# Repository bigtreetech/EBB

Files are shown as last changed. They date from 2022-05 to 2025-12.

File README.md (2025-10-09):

# [切换到中文版](./README_zh_cn.md)

# EBB36 & 42 CAN V1.0
## Hardware
* MCU: ARM Cortex-M0 STM32F072C8T6 48MHz with CAN bus
* Stepper Dirver: Onboard TMC2209 in UART mode, UART address: 00, Rsense: 0.11R
* Onboard Accelerometer Sensor: ADXL345
* Onboard Temperature IC: Max31865 Select 2 / 4 lines PT100 / PT1000 by DIP switch (no Max31865 verson have not this feature)
* Input Voltage: DC12V-DC24V 6A
* Logic Voltage: DC 3.3V
* Heating Interface: Hotend (E0), maximum output current: 5A
* Fan Interfaces: two CNC fans (FAN0, FAN1)
* Maximum Output Current of Fan Interface: 1A, Peak Value 1.5A
* Expansion Interfaces: EndStop, I2C, Probe, RGB, PT100/PT1000, USB interface, CAN Interface
* Temperature Sensor Interface Optional: 1 Channel 100K NTC or PT1000(TH0), 1 Channel PT100/PT1000
* USB Communication Interface: USB-Type-C
* DC 5V Maximum Output Current: 1A

## Firmware
* Only supports Klipper at the present.

## Pinout
* EBB36 CAN V1.0
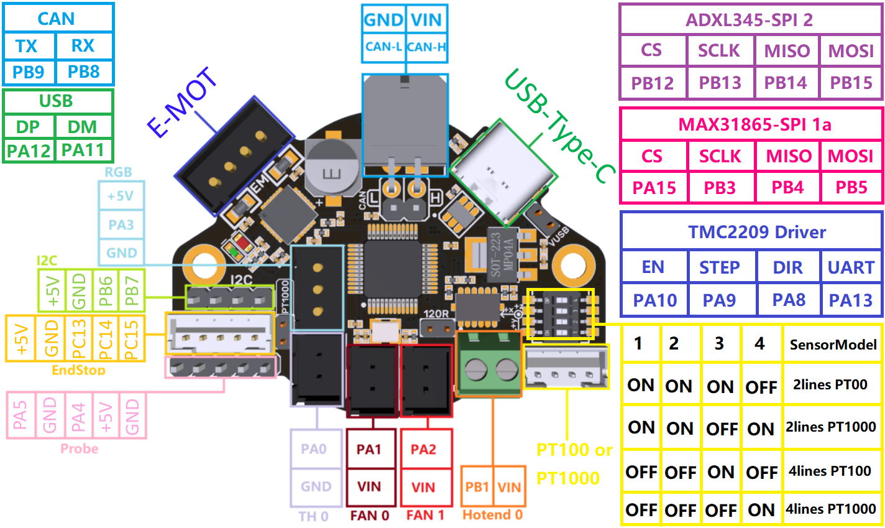
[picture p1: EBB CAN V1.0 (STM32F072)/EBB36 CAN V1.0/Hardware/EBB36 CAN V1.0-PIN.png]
  <br/><br/>
* EBB42 CAN V1.0
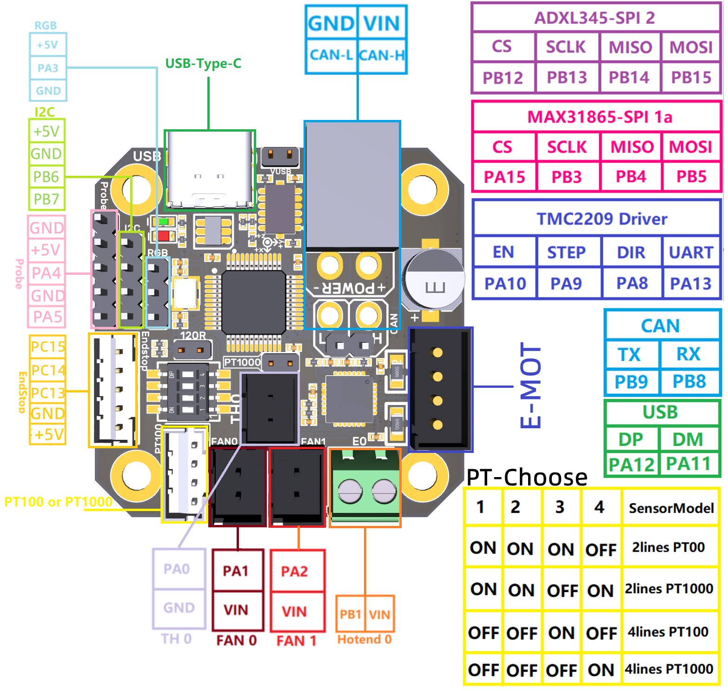
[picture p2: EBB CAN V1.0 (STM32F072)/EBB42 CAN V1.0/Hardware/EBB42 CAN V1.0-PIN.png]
  <br/><br/>

## Build Firmware Image
1. Precompiled firmware(The source code version used is [Commits on Nov 20, 2023](https://github.com/Klipper3d/klipper/commit/bb4711c5d31e8159945f945c662e6668059a174f))
   * [firmware_USB.bin](./EBB%20CAN%20V1.0%20(STM32F072)/firmware_USB.bin) Use USB to communicate with raspberry pi / BTT Pi.
   * [firmware_canbus.bin](./EBB%20CAN%20V1.0%20(STM32F072)/firmware_canbus.bin) Use CAN bus to communicate with raspberry pi / BTT Pi, baudrate = 1000K.

3. Build your own firmware<br/>
   1. Refer to [klipper's official installation](https://www.klipper3d.org/Installation.html) to download klipper source code to raspberry pi
   2. `Building the micro-controller` with the configuration shown below.
      * [*] Enable extra low-level configuration options
      * Micro-controller Architecture = `STMicroelectronics STM32`
      * Processor model = `STM32F072`
      * IF USE CanBoot
         * Bootloader offset = `8KiB bootloader`
      * ELSE
         * Bootloader offset = `No bootloader`
      * Clock Reference = `8 MHz crystal`
      * IF USE USB
         * Communication interface = `USB (on PA11/PA12)`
      * ElSE IF USE CAN bus
         * Communication interface = `CAN bus (on PB8/PB9)`
         * `(1000000)` CAN bus speed

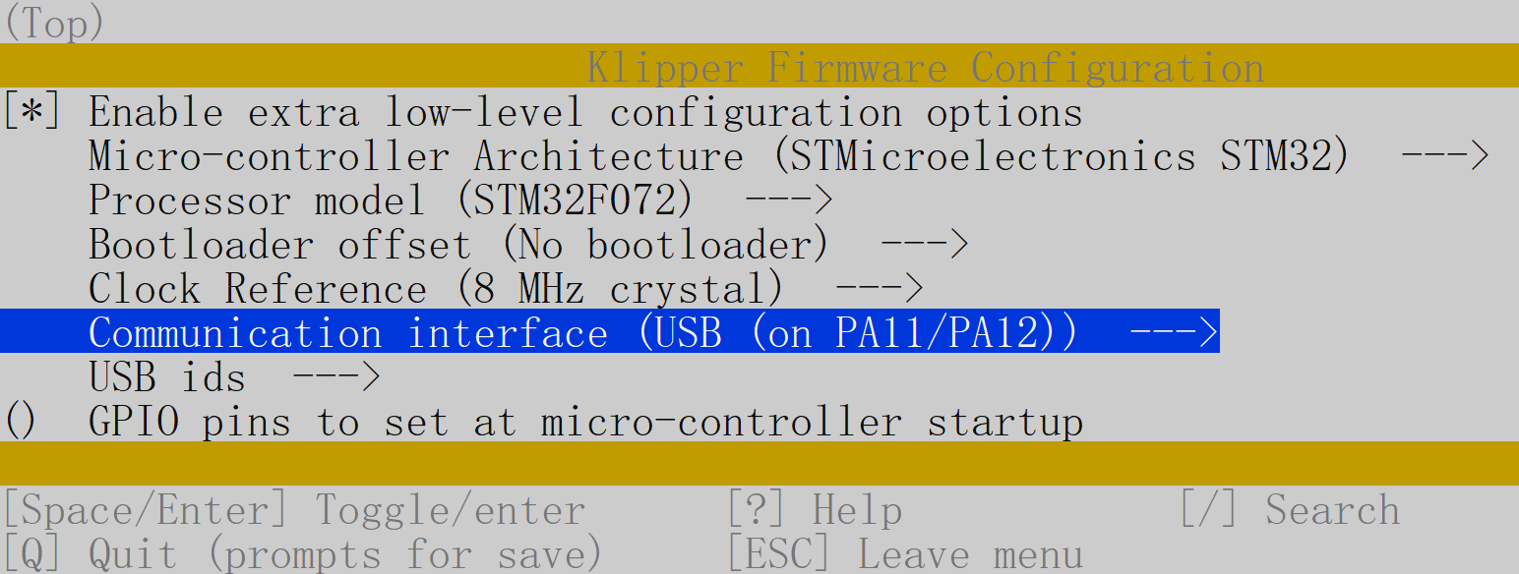
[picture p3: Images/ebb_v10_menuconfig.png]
      <br/>
   3. Once the configuration is selected, press `q` to exit,  and "Yes" when  asked to save the configuration.
   4. Run the command `make`
   5. The `klipper.bin` file will be generated in the folder `home/pi/kliiper/out` when the `make` command completed. And you can use the windows computer under the same LAN as raspberry pi to copy `klipper.bin` from raspberry pi to the computer with `pscp` command in the CMD terminal. such as `pscp -C pi@192.168.0.101:/home/pi/klipper/out/klipper.bin c:\klipper.bin`(The terminal may prompt that `The server's host key is not cached` and ask `Store key in cache?((y/n)`, Please type `y` to store. And then it will ask for a password, please type the default password `raspberry` for raspberry pi)

## board.cfg files
   * [sample-bigtreetech-ebb-canbus-v1.0.cfg](./EBB%20CAN%20V1.0%20(STM32F072)/sample-bigtreetech-ebb-canbus-v1.0.cfg) includes all the correct pinout for EBB36 & 42 CAN V1.0

# EBB36 & 42 CAN V1.1 and V1.2
## Hardware
* MCU: ARM Cortex-M0+ STM32G0B1CBT6 64MHz whit FDCAN bus
* All other parameters are the same as EBB36 & 42 CAN V1.0

## Firmware
* Only supports Klipper at the present.

## Pinout
* EBB36 CAN V1.1 and V1.2
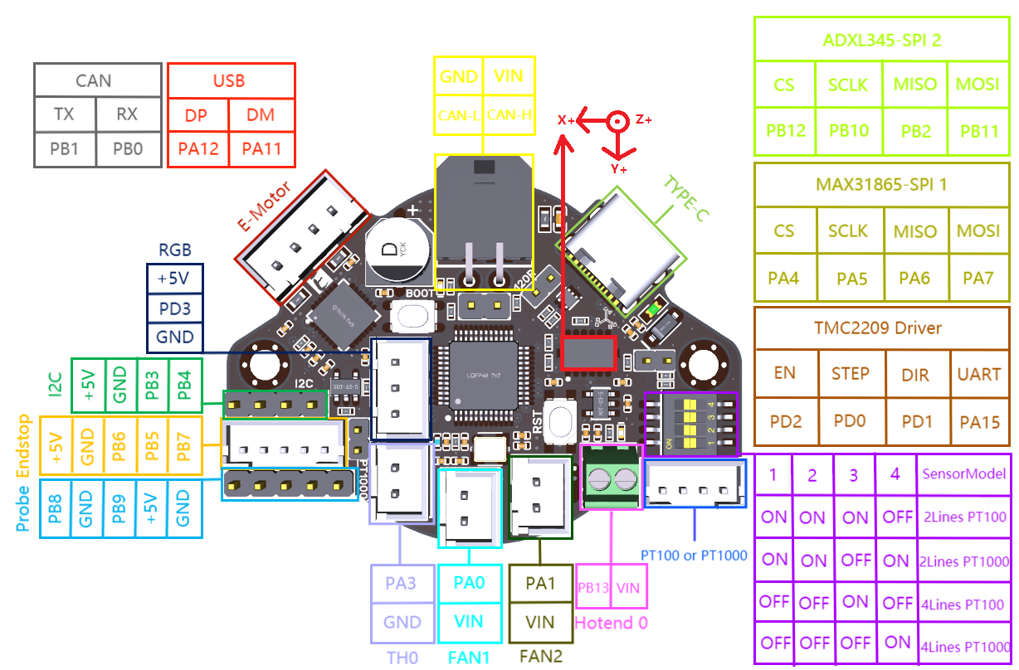
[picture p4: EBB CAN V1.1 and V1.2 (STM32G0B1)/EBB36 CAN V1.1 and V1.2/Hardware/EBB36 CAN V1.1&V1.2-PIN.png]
  <br/><br/>
* EBB42 CAN V1.1 and V1.2
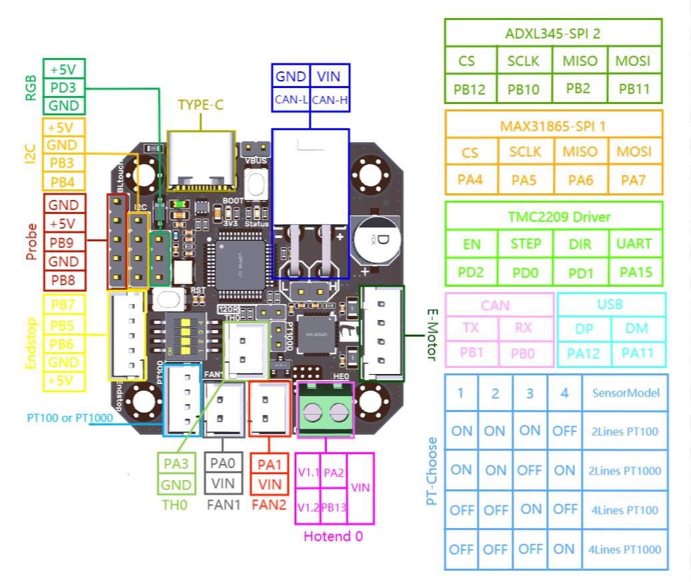
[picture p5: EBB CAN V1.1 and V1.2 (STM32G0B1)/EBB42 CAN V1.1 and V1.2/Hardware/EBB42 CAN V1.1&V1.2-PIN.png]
  <br/><br/>

## Build Firmware Image
1. Precompiled firmware(The source code version used is [Commits on Nov 20, 2023](https://github.com/Klipper3d/klipper/commit/bb4711c5d31e8159945f945c662e6668059a174f))
   * [firmware_USB.bin](./EBB%20CAN%20V1.1%20and%20V1.2%20(STM32G0B1)/firmware_USB.bin) Use USB to communicate with raspberry pi.
   * [firmware_canbus.bin](./EBB%20CAN%20V1.1%20and%20V1.2%20(STM32G0B1)/firmware_canbus.bin) Use CAN bus to communicate with raspberry pi, baudrate = 1000K.

3. Build your own firmware<br/>
   1. Refer to [klipper's official installation](https://www.klipper3d.org/Installation.html) to download klipper source code to raspberry pi
   2. `Building the micro-controller` with the configuration shown below.
      * [*] Enable extra low-level configuration options
      * Micro-controller Architecture = `STMicroelectronics STM32`
      * Processor model = `STM32G0B1`
      * IF USE CanBoot
         * Bootloader offset = `8KiB bootloader`
      * ELSE
         * Bootloader offset = `No bootloader`
      * Clock Reference = `8 MHz crystal`
      * IF USE USB
         * Communication interface = `USB (on PA11/PA12)`
      * ElSE IF USE CAN bus
         * Communication interface = `CAN bus (on PB0/PB1)`
         * `(1000000)` CAN bus speed

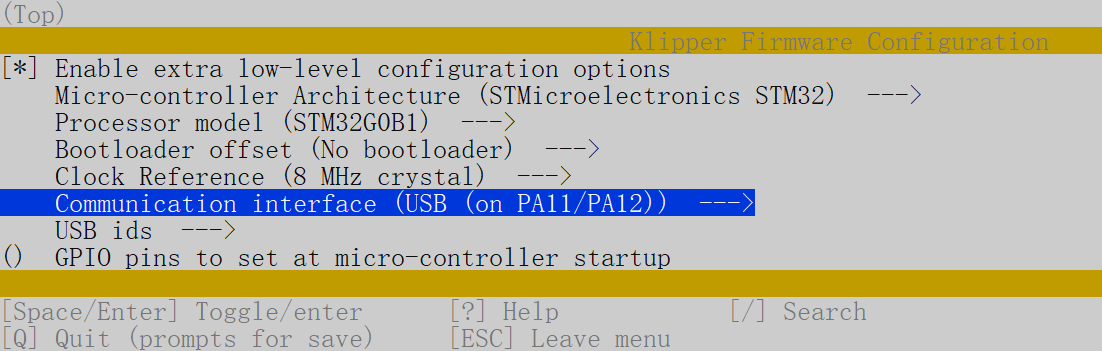
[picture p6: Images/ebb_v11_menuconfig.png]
      <br/>
   3. Once the configuration is selected, press `q` to exit,  and "Yes" when  asked to save the configuration.
   4. Run the command `make`
   5. The `klipper.bin` file will be generated in the folder `home/pi/kliiper/out` when the `make` command completed. And you can use the windows computer under the same LAN as raspberry pi to copy `klipper.bin` from raspberry pi to the computer with `pscp` command in the CMD terminal. such as `pscp -C pi@192.168.0.101:/home/pi/klipper/out/klipper.bin c:\klipper.bin`(The terminal may prompt that `The server's host key is not cached` and ask `Store key in cache?((y/n)`, Please type `y` to store. And then it will ask for a password, please type the default password `raspberry` for raspberry pi)

## Firmware update
### Warning: <br/>
(Only for EBB 36/42 CAN V1.1)<br/>
__STM32G0B1CB needs to jump to the System memory area to run bootloader (written by STMicroelectronics) when using DFU to update firmware through the Type-C port. Referring to the description in manual [AN2606](https://www.st.com/content/ccc/resource/technical/document/application_note/b9/9b/16/3a/12/1e/40/0c/CD00167594.pdf/files/CD00167594.pdf/jcr:content/translations/en.C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), The initialization process of this bootloader is shown in the following figure:__
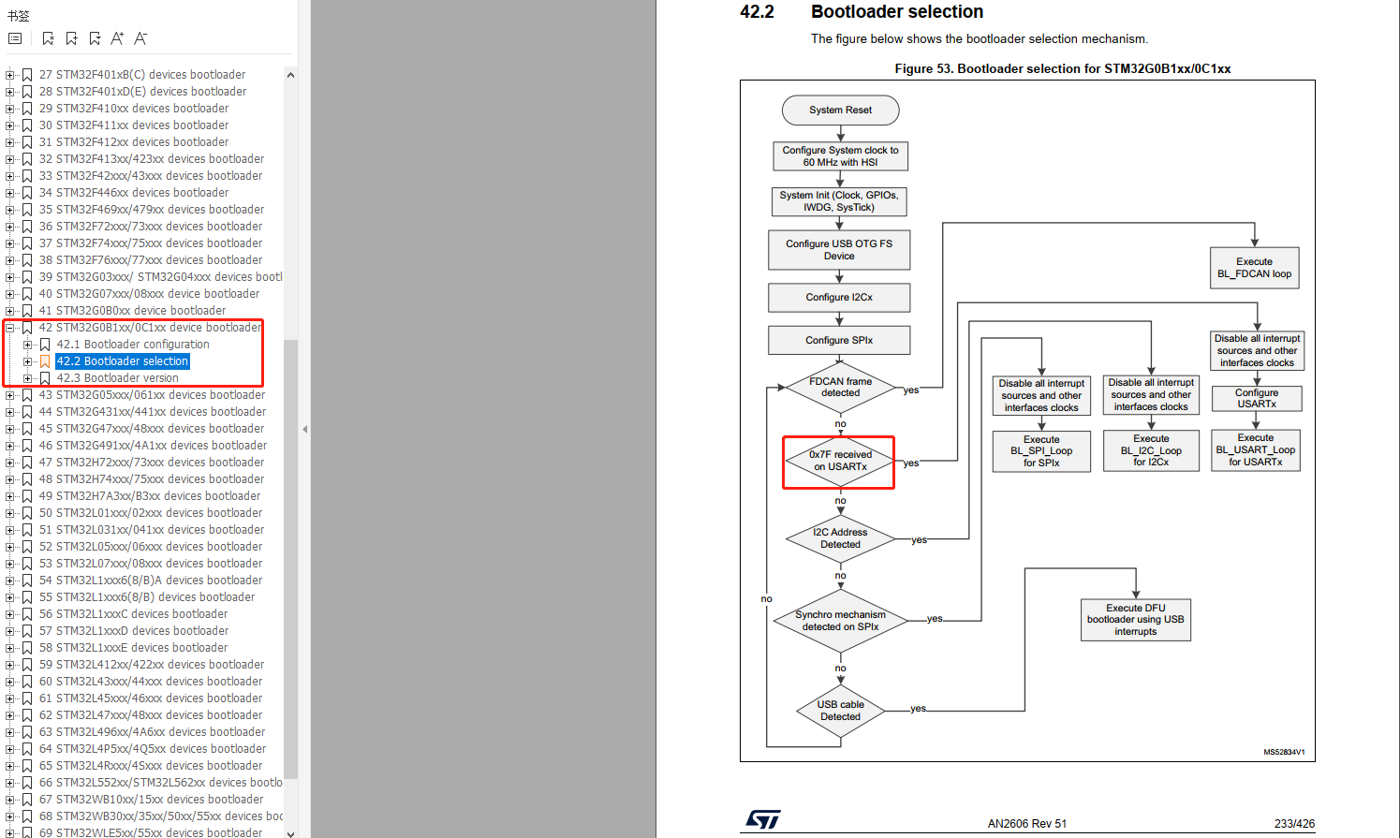
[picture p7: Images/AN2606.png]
  <br/><br/>
__The IO of USART will be configured before going to the USB DFU mode.__<br/>
__After going to DFU mode, PA2 will be configured to output high level by bootloader in System memory area refer to the [datasheet of STM32G0B1CB](https://www.st.com/resource/en/datasheet/stm32g0b1cb.pdf)__
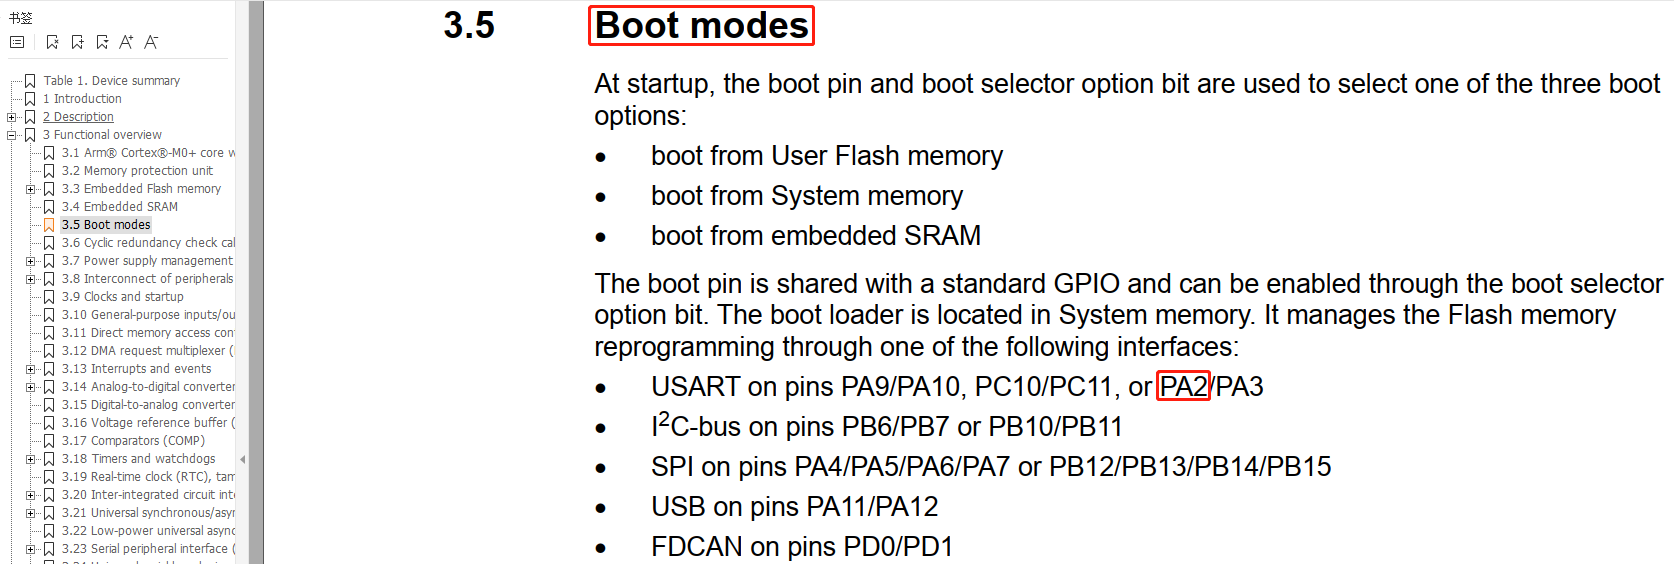
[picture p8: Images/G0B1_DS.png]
  <br/><br/>
__PA2 is used for the hotend MOSFET in EBB36 & 42 CAN V1.1, The high level in the DFU mode change the hotend into heating state. Therefore, please pay attention to disconnect the main power VIN of the hotend when using the DFU of Type-C port to update the firmware, or ensure that the firmware update is completed soon and goto the normal working mode. Never keep MCU in DFU mode for a long time when the main power supply and hotend are connected.__
## board.cfg files
   * [sample-bigtreetech-ebb-canbus-v1.1.cfg](./EBB%20CAN%20V1.1%20and%20V1.2%20(STM32G0B1)/sample-bigtreetech-ebb-canbus-v1.1.cfg) includes all the correct pinout for EBB CAN 36&42 V1.1

# EBB36 & 42 CAN V1.2
__V1.2 compared with v1.1: only the IO of hotend is changed from `PA2` to `PB13`__

## board.cfg files
   * [sample-bigtreetech-ebb-canbus-v1.2.cfg](./EBB%20CAN%20V1.1%20and%20V1.2%20(STM32G0B1)/sample-bigtreetech-ebb-canbus-v1.2.cfg) includes all the correct pinout for EBB CAN 36&42 V1.2

# EBB SB2240_2209 CAN V1.0
## Hardware
* MCU: ARM Cortex-M0+ STM32G0B1CBT6 64MHz whit FDCAN bus
* Stepper Dirver:
   * TMC2209 Version: Onboard TMC2209 in UART mode, UART address: 00, Rsense: 0.11R
   * TMC2240 Version: Onboard TMC2240 in SPI mode
* Onboard Accelerometer Sensor: ADXL345
* Onboard Temperature IC: Max31865 Select 2 / 4 lines PT100 / PT1000 by DIP switch
* Input Voltage: DC12V-DC24V 9A
* Logic Voltage: DC 3.3V
* Heating Interface: Hotend (E0), maximum output current: 5A
* Fan Interfaces:
   * 2 x CNC fans (FAN1, FAN2)
   * 1 x 4-wire fan (4W_FAN)
* Maximum Output Current of Fan Interface: 1A, Peak Value 1.5A
* Expansion Interfaces: EndStop, Bltouch, Proximity(NPN & PNP), RGB, PT100/PT1000, USB, CAN, SPI
* Temperature Sensor Interface Optional: 1 Channel 100K NTC or PT1000(TH0), 1 Channel PT100/PT1000 (Max31865)
* USB Communication Interface: USB-Type-C
* DC 5V Maximum Output Current: 1A

## Firmware
* Only supports Klipper at the present.

## Pinout
* EBB SB2240 CAN V1.0
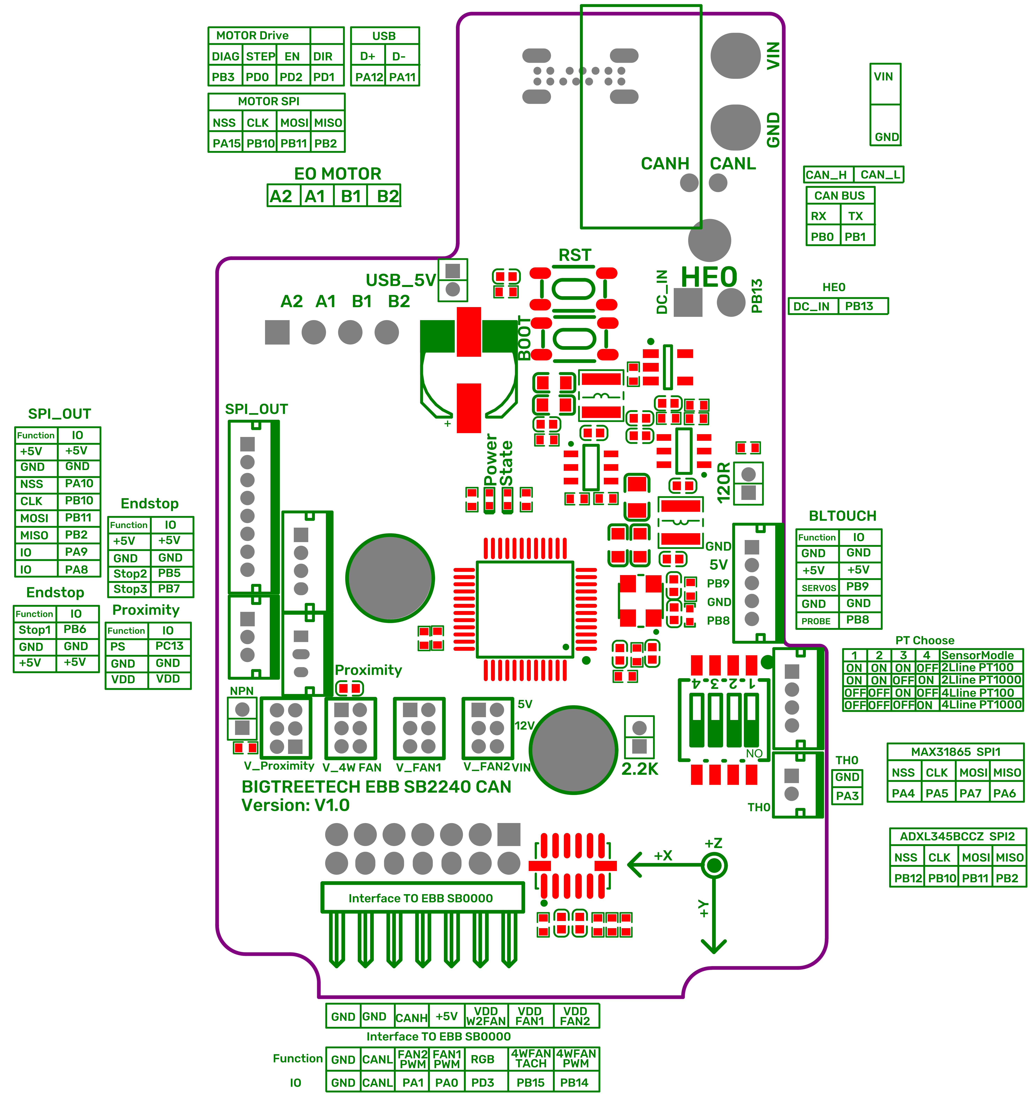
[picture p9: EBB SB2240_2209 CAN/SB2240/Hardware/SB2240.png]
  <br/><br/>
* EBB SB2209 CAN V1.0
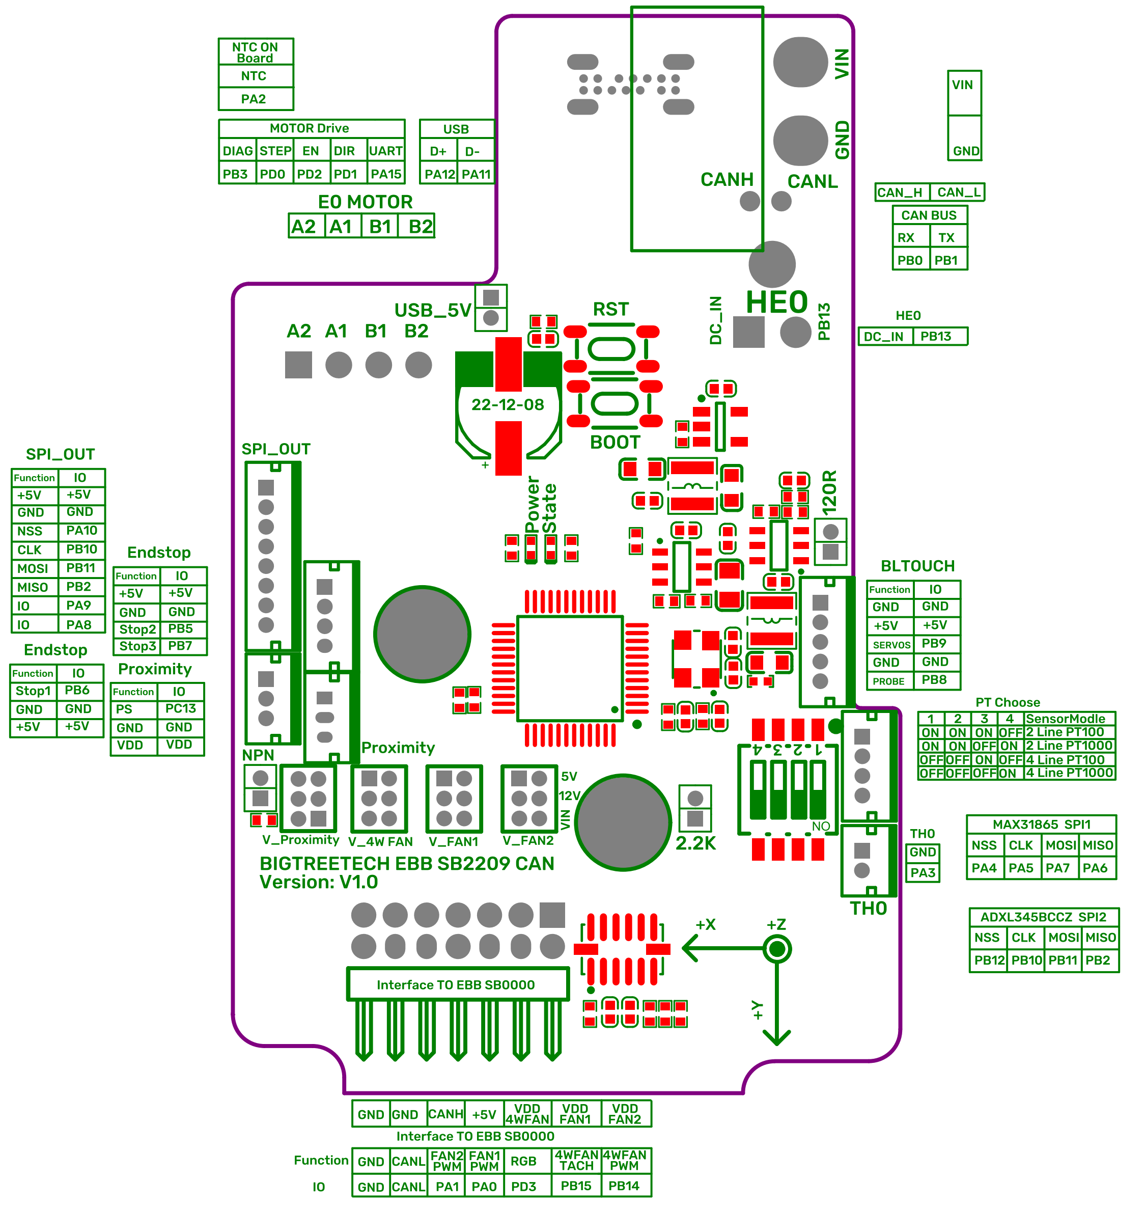
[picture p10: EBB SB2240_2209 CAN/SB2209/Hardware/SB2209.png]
  <br/><br/>

## Build Firmware Image
1. Precompiled firmware(The source code version used is [Commits on Jan 8, 2023](https://github.com/Klipper3d/klipper/commit/bca2671efb8ae6035bb8600619b7a7c4e76169c3))
   * [firmware_USB.bin](./EBB%20SB2240_2209%20CAN/firmware_USB.bin) Use USB to communicate with host.
   * [firmware_canbus.bin](./EBB%20SB2240_2209%20CAN/firmware_canbus.bin) Use CAN bus to communicate with host, baudrate = 1M.
   * [firmware_canbus_8k_bootloader.bin](./EBB%20SB2240_2209%20CAN/firmware_canbus_8k_bootloader.bin) Use CAN bus to communicate with host, baudrate = 1M, 8KB bootloader for Canboot.

3. Build your own firmware<br/>
   1. Refer to [klipper's official installation](https://www.klipper3d.org/Installation.html) to download klipper source code to host
   2. `Building the micro-controller` with the configuration shown below.
      * [*] Enable extra low-level configuration options
      * Micro-controller Architecture = `STMicroelectronics STM32`
      * Processor model = `STM32G0B1`
      * IF USE CanBoot
         * Bootloader offset = `8KiB bootloader`
      * ELSE
         * Bootloader offset = `No bootloader`
      * Clock Reference = `8 MHz crystal`
      * IF USE USB
         * Communication interface = `USB (on PA11/PA12)`
      * ElSE IF USE CAN bus
         * Communication interface = `CAN bus (on PB0/PB1)`
      * (1000000) CAN bus speed

      <br/>
   3. Once the configuration is selected, press `q` to exit,  and "Yes" when  asked to save the configuration.
   4. Run the command `make`
   5. The `klipper.bin` file will be generated in the folder `home/pi/kliiper/out` when the `make` command completed. And you can use the windows computer under the same LAN as host to copy `klipper.bin` from host to the computer with `pscp` command in the CMD terminal. such as `pscp -C pi@192.168.0.101:/home/pi/klipper/out/klipper.bin c:\klipper.bin`(The terminal may prompt that `The server's host key is not cached` and ask `Store key in cache?((y/n)`, Please type `y` to store. And then it will ask for a password, please type the default password `raspberry` for raspberry pi or `biqu` for CB1)

## board.cfg files
   * [sample-bigtreetech-ebb-sb-canbus-v1.0.cfg](./EBB%20SB2240_2209%20CAN/sample-bigtreetech-ebb-sb-canbus-v1.0.cfg) includes all the correct pinout for EBB SB2240_2209 CAN V1.0
   * TMC2209 Version: uncomment tmc2209 config and comment tmc2240 config
      ```
      [tmc2209 extruder]
      uart_pin: EBBCan: PA15
      run_current: 0.650
      stealthchop_threshold: 999999

      # [tmc2240 extruder]
      # cs_pin: EBBCan: PA15
      # spi_bus: spi2_PB2_PB11_PB10
      # run_current: 0.650
      # stealthchop_threshold: 999999
      ```
   * TMC2240 Version: uncomment tmc2240 config and comment tmc2209 config
      ```
      # [tmc2209 extruder]
      # uart_pin: EBBCan: PA15
      # run_current: 0.650
      # stealthchop_threshold: 999999

      [tmc2240 extruder]
      cs_pin: EBBCan: PA15
      # spi_bus: spi2_PB2_PB11_PB10
      driver_TPFD: 0
      run_current: 0.650
      stealthchop_threshold: 999999
      ```

# Note
## Here’s BIGTREETECH! For Makers, by makers!
* We appreciate all of your support to BIGTREETECH! To offer an excellent experience of creation to every makers,We’re devoted to design and produce high-quality and durable accessories!

## How to contact:
### If you have any technical issue,please don’t hesitate contact us:
* BIGTREETECH: service004@biqu3d.com

### Follow us on social media to get more news:
* Facebook: https://www.facebook.com/BIGTREETECH/
* Twitter: https://twitter.com/BigTreeTech
* Instagram: https://www.instagram.com/bigtreetech_official/
* Official Site: https://bigtree-tech.com/

## Purchase link:
https://www.biqu.equipment/products/bigtreetech-ebb-36-42-can-bus-for-connecting-klipper-expansion-device

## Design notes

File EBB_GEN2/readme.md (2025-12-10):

# User Manuals
For user manuals on the Gen 2 boards, please consult our wiki at [global.bttwiki.com](https://global.bttwiki.com)

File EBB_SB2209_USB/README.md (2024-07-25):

# EBB SB2209 USB

[English](README.md "change to English langue") | [简体中文](README_ZH.md "change to chinese langue")

### Getting Started
To ensure the full functionality and stability of the product, when using the EBB SB2209 USB product, we recommend downloading and printing the STL files from this document for assembly. If you need further development of the printed parts, you can use the Step files provided in the CAD folder.

### Compatibility of Printed Parts
* **PCB_Spacer_EBB-SB-USB Printed Part:** This printed part is required for installing the EBB SB2209 USB product to be compatible with other original VORON Stealthburner printed parts. It is also compatible with the printed parts required for the installation of the EBB SB CAN product. Additionally, you can continue to use the original VORON Stealthburner PCB_Spacer without downloading this printed part, but we do not recommend this as it may slightly interfere with the optical coupler.
* **Main_Body_EBB-SB-USB and Cable_Cover_EBB-SB-USB Printed Parts:** Both of these printed parts must be used together for installing the EBB SB2209 USB product to be compatible with other original VORON Stealthburner printed parts. They are also required for the installation of the EBB SB CAN product. If used separately, there will be interference issues. Please download and use both printed parts together.
* **Cable_Cover_EBB-SB-USB Printed Part:** This printed part is required for installing the EBB SB2209 USB product. Using the original Cable_Cover on the VORON Stealthburner might result in incomplete closure.

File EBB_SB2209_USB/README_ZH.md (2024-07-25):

# EBB SB2209 USB

[English](README.md "change to English langue") | [简体中文](README_ZH.md "change to chinese langue")

### 开始使用
为了保证产品功能的充分发挥和运行的稳定性，当您使用EBB SB2209 USB产品时，我们建议您下载并打印本文件中的STL文件进行装配。如果您对装配的打印件有进一步的开发需求，可以使用我们在CAD文件夹中提供的Step文件。
### 打印件兼容性
* **PCB_Spacer_EBB-SB-USB打印件：** EBB SB2209 USB产品安装时需使用此打印件，方可兼容装配至VORON Stealthburner其他原版打印件上，同时该打印件亦兼容EBB SB CAN产品安装所另外，您可以继续沿着使用 VORON Stealthburner 原版 PCB_Spacer 而无需下载此打印件使用，但我们不建议您如此处理，其会与光耦合有轻微关联。
* **Main_Body_EBB-SB-USB和Cable_Cover_EBB-SB-USB打印件：** EBB SB2209 USB产品安装必须同时使用此两打印件，方可兼容装配至VORON Stealthburner其他原版打印件上，同时亦EBB SB CAN产品安装所需打印件。如单独使用将存在问题，请同时下载这两个打印件使用。
* **Cable_Cover_EBB-SB-USB 打印件：** EBB SB2209 USB 产品安装必须使用该打印件，如使用 VORON Stelthbunner 上原版的 Cable_Cover 可能会有无法完全闭合的情况。

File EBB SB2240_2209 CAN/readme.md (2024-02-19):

### Printed_Part_for_CAN_Cable_V1.2
* 优化开槽，修正与现有版本CAN线插头外形差异的问题，使其更加贴合可靠。
* The slot is optimized to fit the existing CAN cable connector better, improving reliability.

### Cable_Cover_EBB	
* Cable_Cover_EBB不兼容Voron官方原版Main_Body，需要与本仓库提供的Main_Body_EBB搭配使用。
* Cable_Cover_EBB is no longer compatible with the Voron original main_body. It needs to be used with the corresponding Main_Body_EBB in this repo.

### Main_Body_EBB		
* Main_Body_EBB是本仓库新增打印件，与本仓库提供的Cable_Cover_EBB搭配使用，兼容除cable cover之外的所有原版StealthBurner打印件，
* Main_body_EBB need to be used with Main_Body_EBB. Compatible with all original StealthBurner printed parts except for the cable cover.

### Printed Part for USB-C Cable		
* 因Type-C接头并非标配，需要用户自行调整该打印件以适配其Type-C接头尺寸。
* This printed part was not originally designed for a Type-C connector. Users will need to modify this printed part file to fit the Type-C connector size.

### Tip/提示
* 其他未提供的打印件均使用官方原装 的StealthBurner 打印部件。 请访问获取：https://github.com/VoronDesign/Voron-Stealthburner
* Other printed parts not provided use the official open source of 
 StealthBurner. Please visit: https://github.com/VoronDesign/Voron-Stealthburner

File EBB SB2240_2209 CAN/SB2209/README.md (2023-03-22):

# NOTE when using CANBus you need to use a Jumper on the 120R Jumper on the SB2209 (and the Mainboard M8P in my example)

See here for config settings:
https://github.com/Esoterical/voron_canbus/tree/main/toolhead_flashing/common_hardware/BigTreeTech%20SB2209%20and%20SB2240

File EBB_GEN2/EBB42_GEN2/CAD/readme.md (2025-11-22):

# CAD

This folder contains STEP files for the parts to aid in creation of mounts. STEP files are provided instead of STL files as they are superior when it comes to mount modeling.

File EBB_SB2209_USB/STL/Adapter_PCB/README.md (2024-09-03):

# PCB ADAPTER PRINT

This print has been designed to use the Voron style heat set, threaded inserts. The dimensions of these are M3 x 5mm diameter x 4mm height.
Screw the PCB into the top --> Mount the top to the base --> Clip the base onto a DIN rail.

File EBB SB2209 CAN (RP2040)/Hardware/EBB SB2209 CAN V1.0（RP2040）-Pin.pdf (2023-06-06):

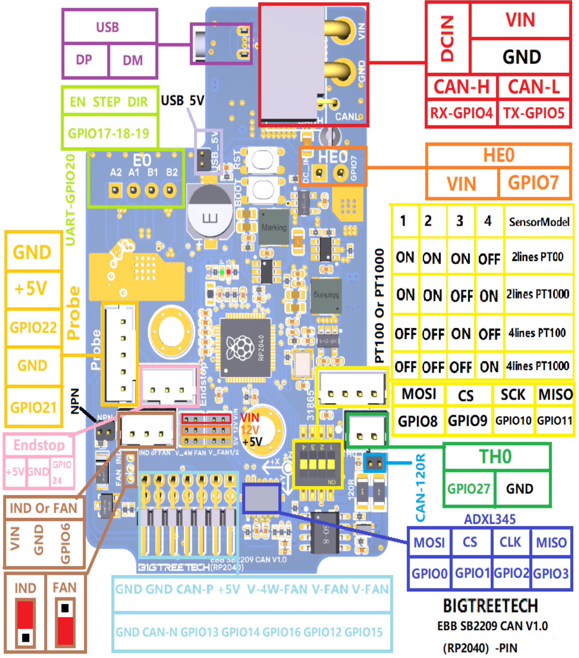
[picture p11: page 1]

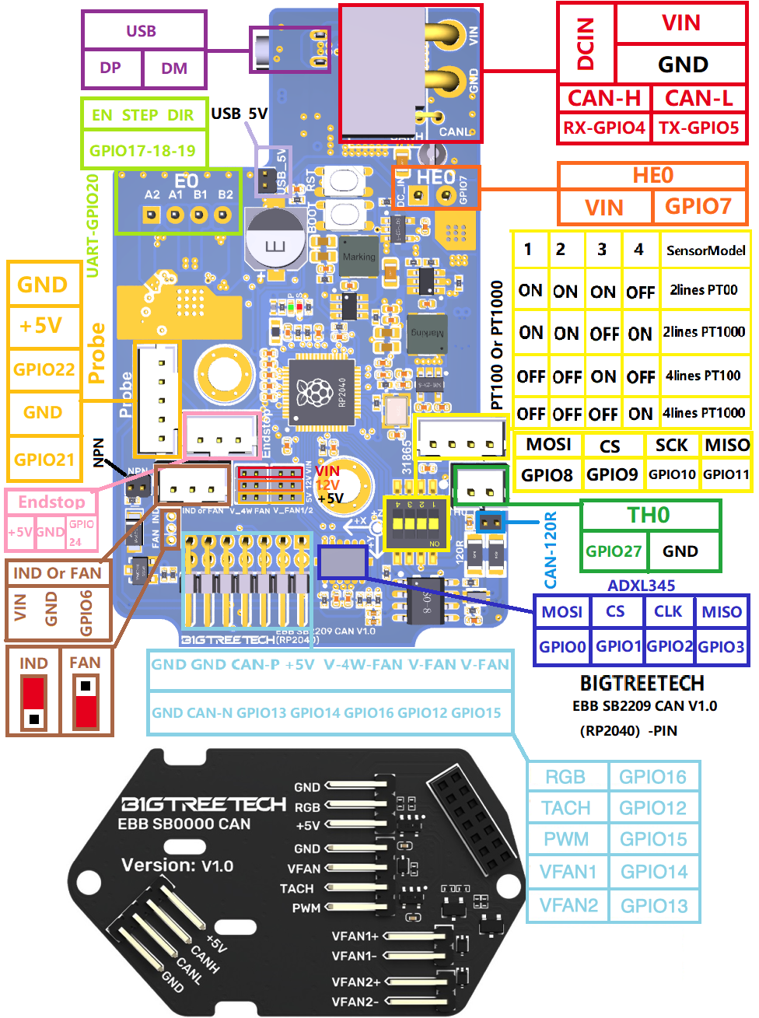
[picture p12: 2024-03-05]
EBB SB2209 CAN (RP2040)/Hardware/EBB SB2209 CAN V1.0（RP2040）-Pin.png

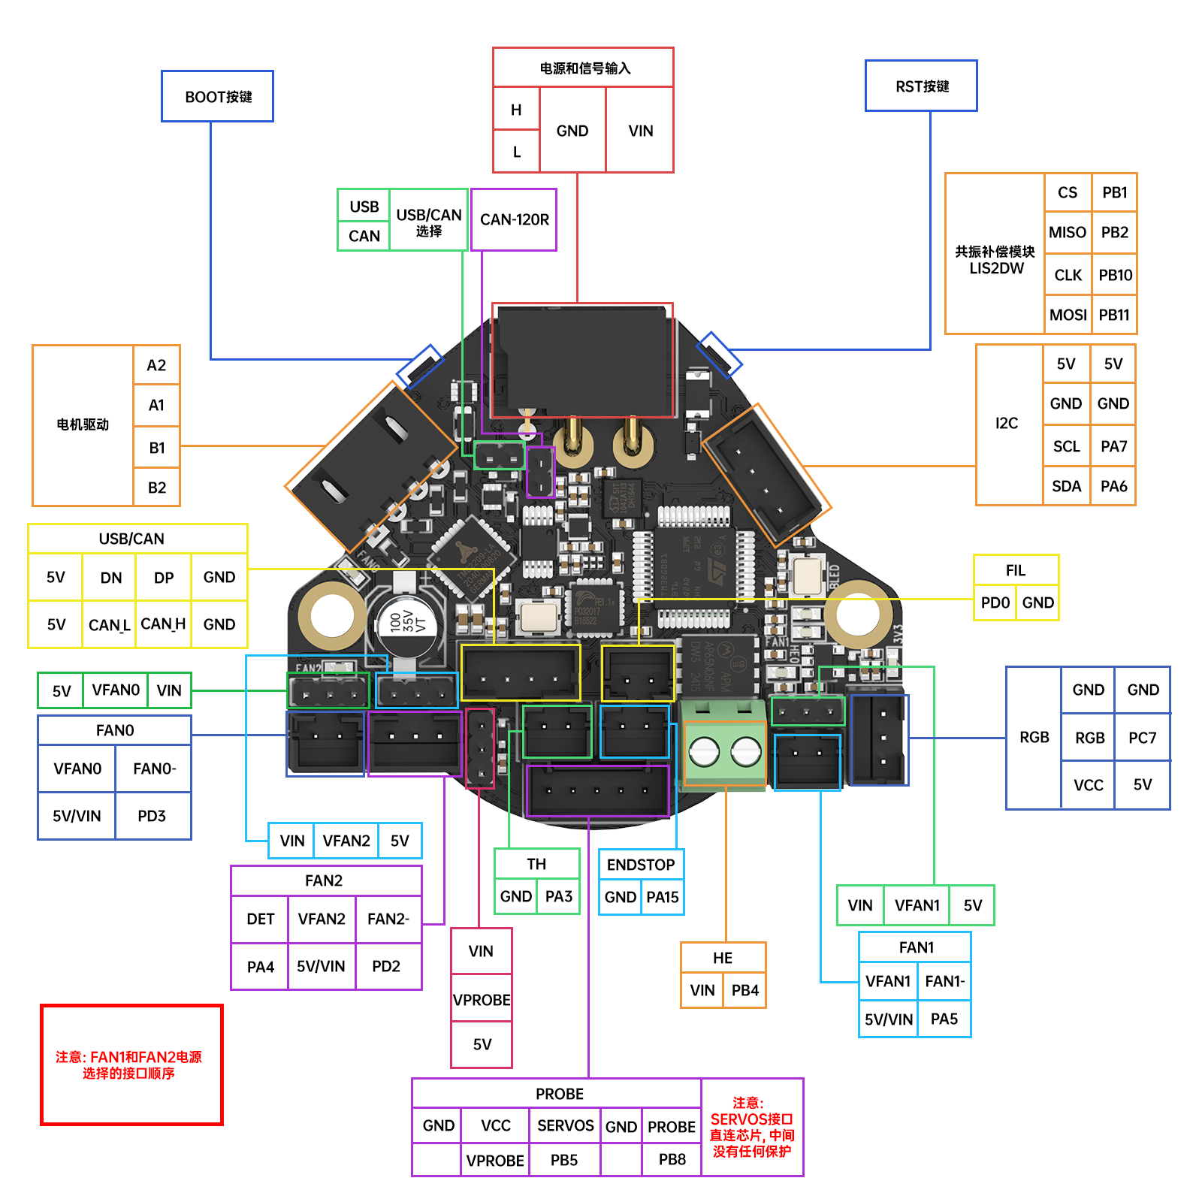
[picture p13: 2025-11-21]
EBB_GEN2/EBB36_GEN2/Hardware/EBB36_GEN2_pin_zh.jpg

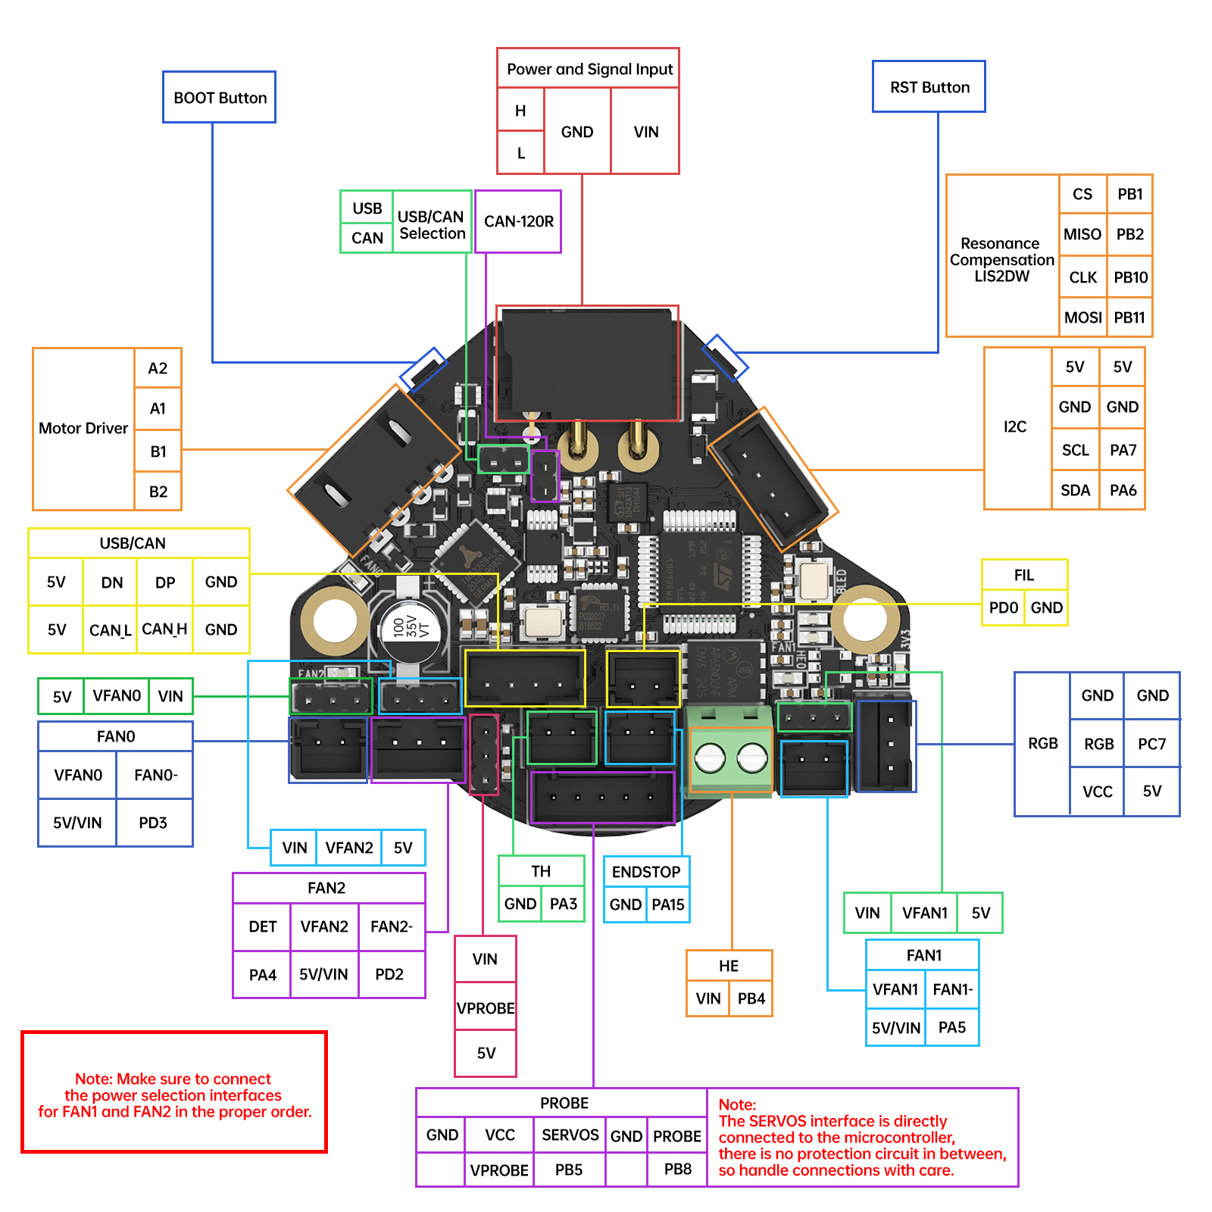
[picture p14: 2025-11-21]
EBB_GEN2/EBB36_GEN2/Hardware/EBB36_GEN2_pin_en.jpg

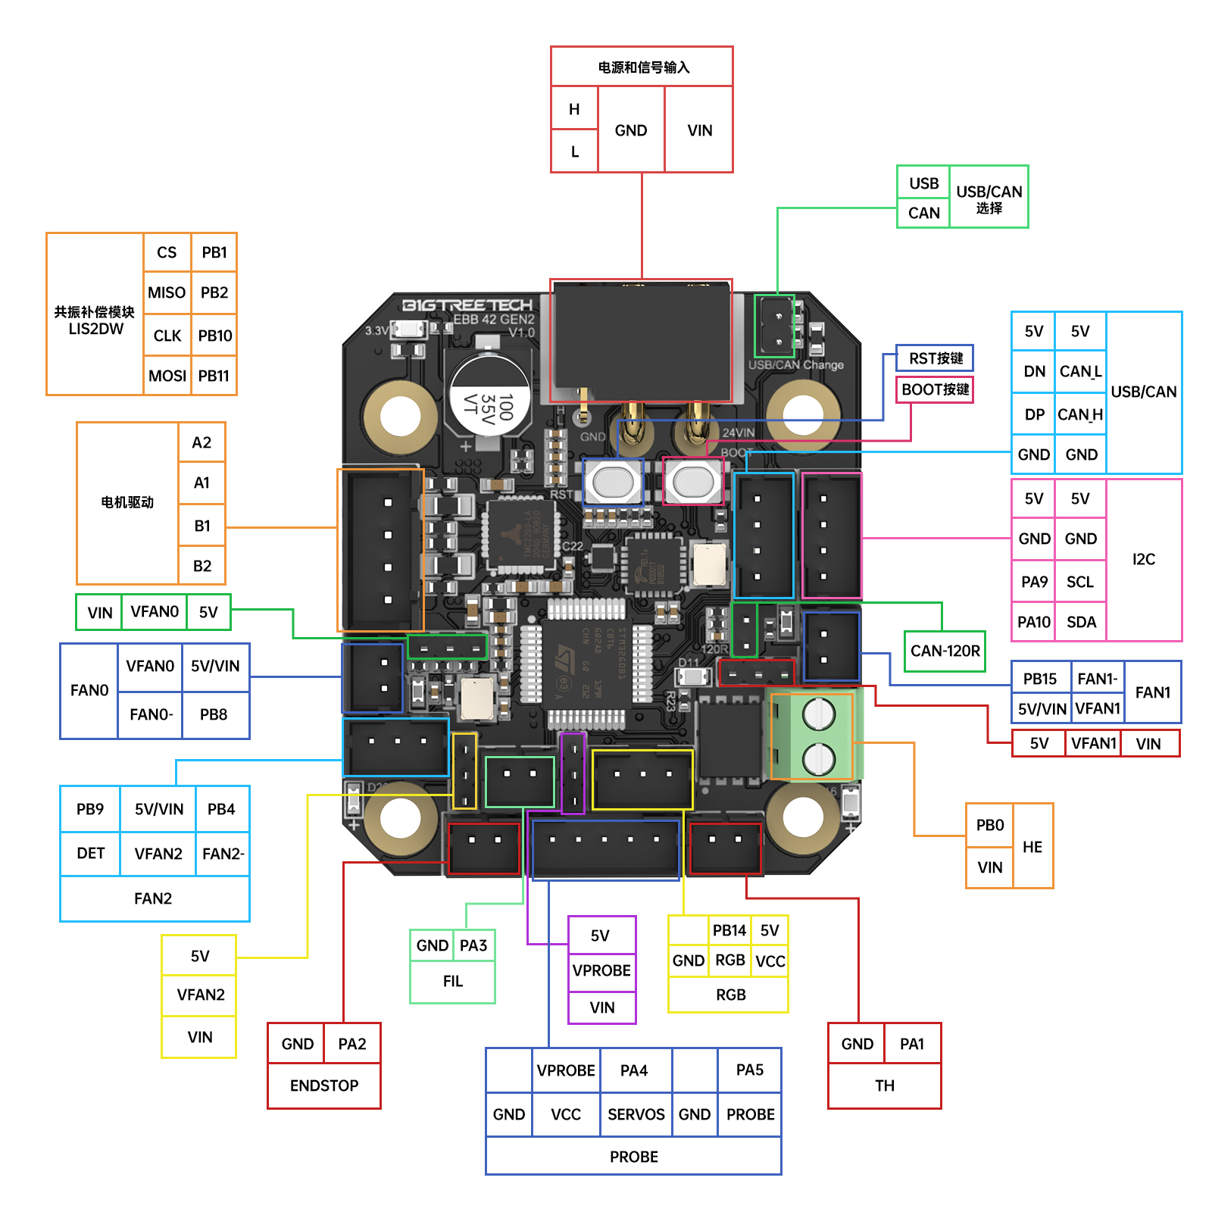
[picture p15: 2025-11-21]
EBB_GEN2/EBB42_GEN2/Hardware/EBB42_GEN2_pin_zh.jpg

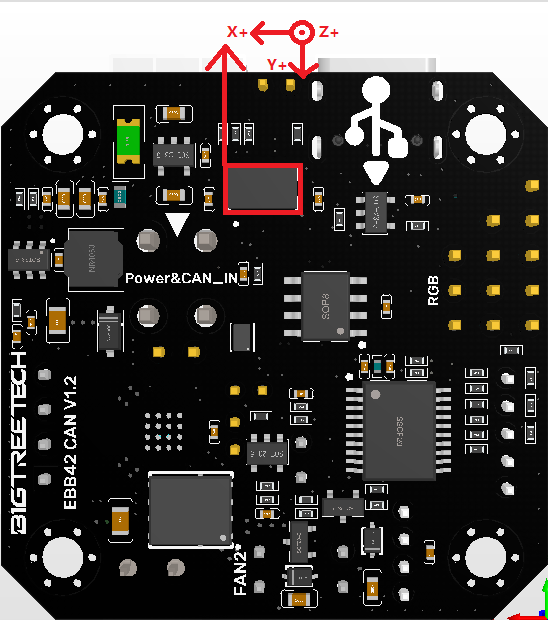
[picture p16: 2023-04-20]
EBB CAN V1.1 and V1.2 (STM32G0B1)/EBB42 CAN V1.1 and V1.2/Hardware/EBB42 CAN V1.1&V1.2-ADXL345.png

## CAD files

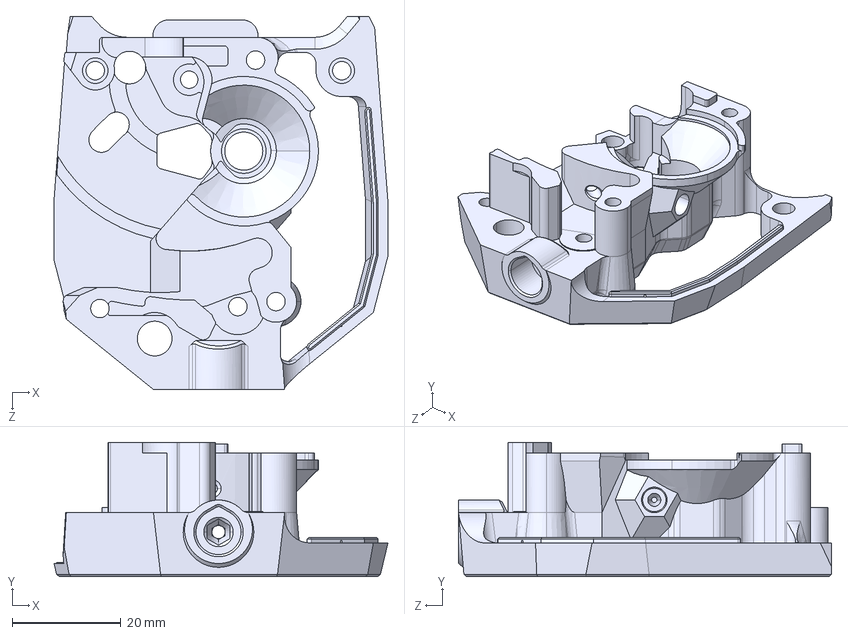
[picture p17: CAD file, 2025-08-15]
EBB_SB2209_USB/CAD/CW2_Printable_Files/cw2_main_boddy_cutting_ecas_EBB-8-25.STEP
61.5 x 24.7 x 68.7 mm

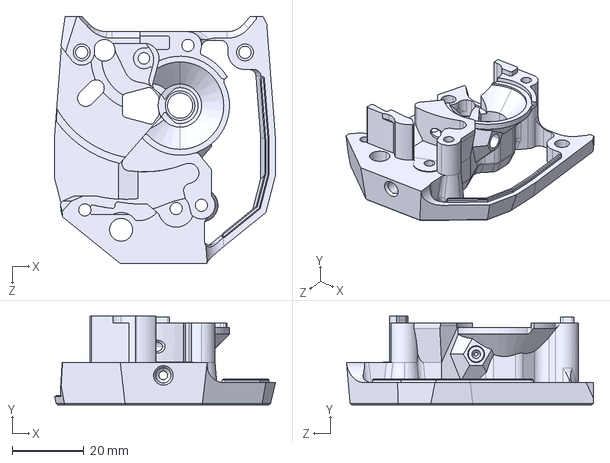
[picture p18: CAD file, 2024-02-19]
EBB SB2240_2209 CAN/CAD/Main_Body_EBB.STEP
61.5 x 24.7 x 68.7 mm

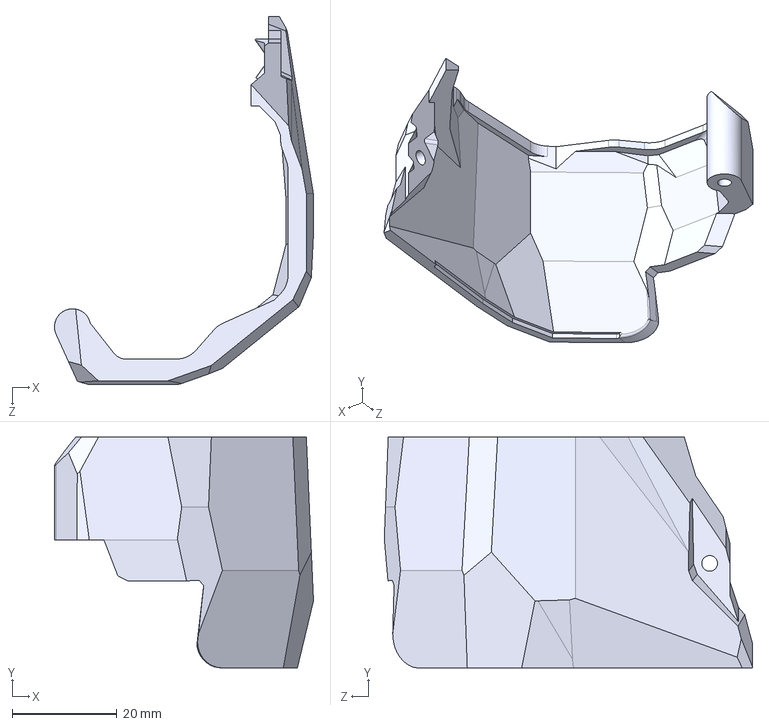
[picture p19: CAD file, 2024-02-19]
EBB SB2240_2209 CAN/CAD/Cable_Cover_EBB.STEP
49.5 x 44.1 x 70.4 mm

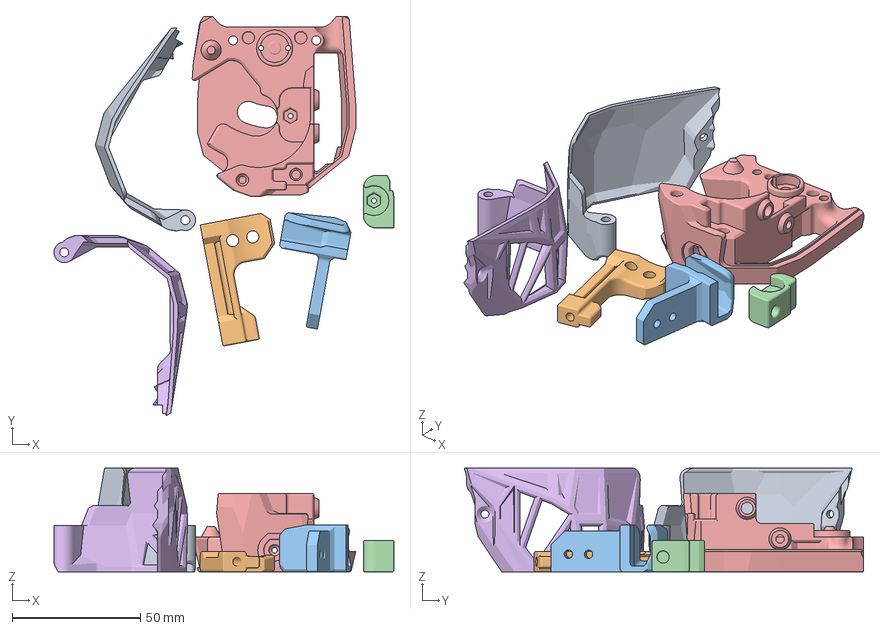
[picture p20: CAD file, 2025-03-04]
EBB_SB2209_USB/CAD/Galileo2_Printable_Files/Beta/Galileo 2-EBB USB.3mf
132.5 x 155.7 x 40.5 mm
Galileo 2 Extruder Cable_Cover-EBB USB.STEP
Galileo 2 Extruder Chain_Anchor -EBB USB.STEP
Galileo 2 Extruder cable clamp-ebbusb.STEP
Galileo 2 Extruder idler_bearing_cover-ebbusb.STEP
Galileo 2 Extruder BODY -EBB USB.STEP
galileo 2 extruder cable_cover-ebb usb1_enhanced_airflow.STEP

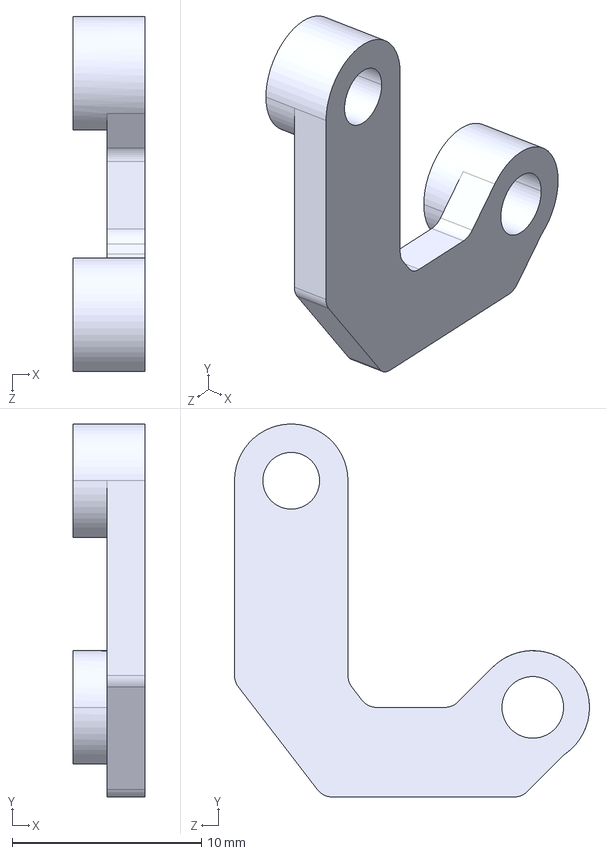
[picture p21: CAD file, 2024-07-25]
EBB_SB2209_USB/CAD/Product_models/PCB_Spacer_EBB-SB-USB.STEP
3.80 x 19.7 x 18.8 mm

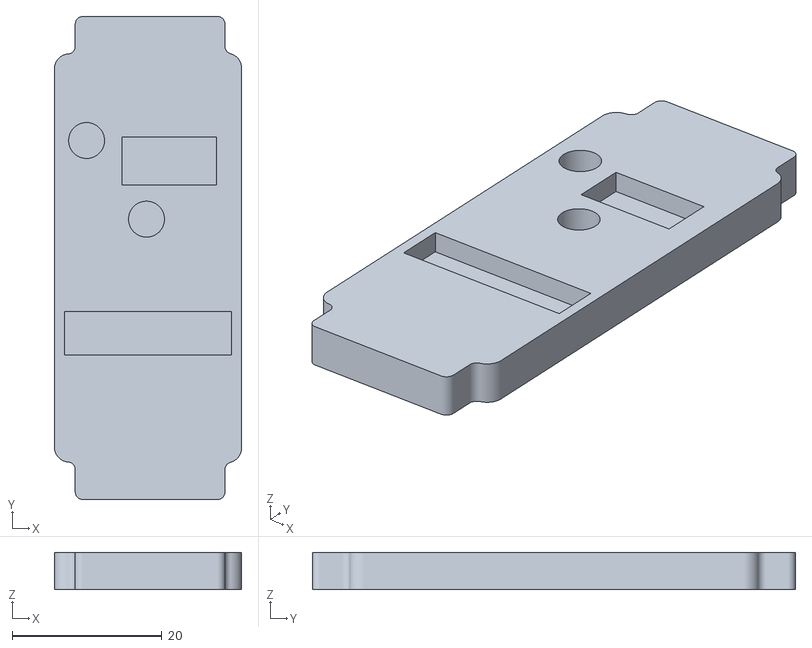
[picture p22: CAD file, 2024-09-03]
EBB_SB2209_USB/STL/Adapter_PCB/EBB_SB2209_ADAPTER_TOP.stl
25.0 x 64.5 x 5.00

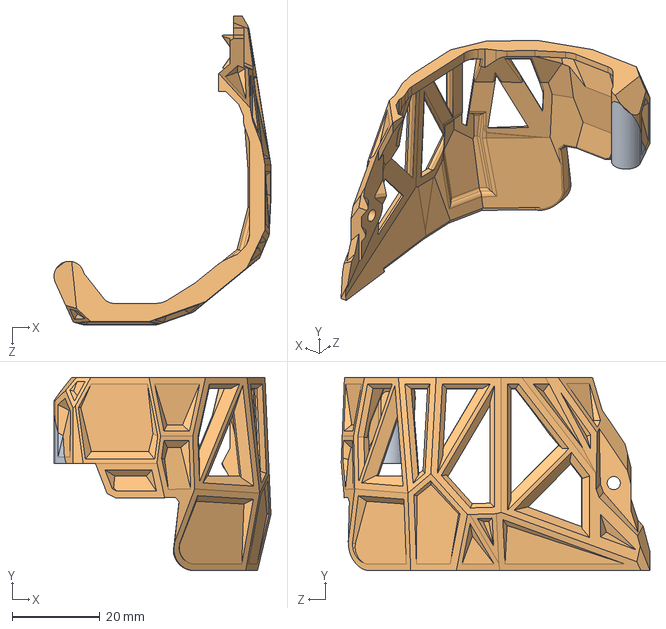
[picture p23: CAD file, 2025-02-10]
EBB_SB2209_USB/CAD/CW2_Printable_Files/Cable_Cover_For_EBBSB1.STEP
49.5 x 44.1 x 70.4 mm

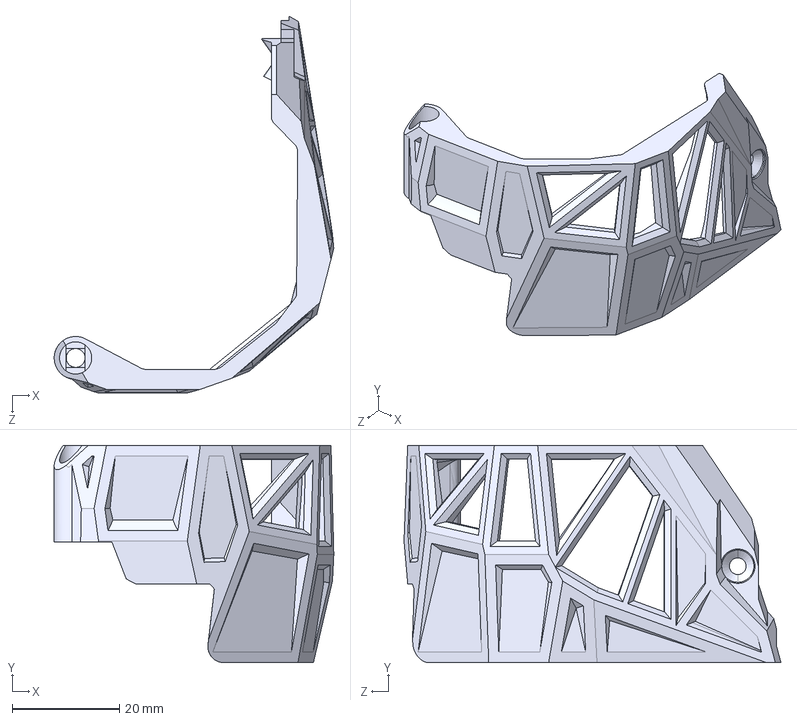
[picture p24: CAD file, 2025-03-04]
EBB_SB2209_USB/CAD/Galileo2_Printable_Files/Beta/galileo 2 extruder cable_cover-ebb usb1_enhanced_airflow.STEP
52.1 x 40.5 x 70.2 mm

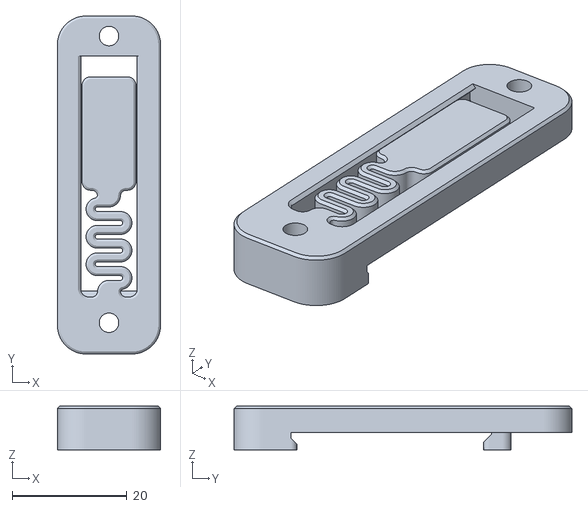
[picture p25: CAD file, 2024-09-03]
EBB_SB2209_USB/STL/Adapter_PCB/EBB_SB2209_ADAPTER_BASE.stl
18.0 x 59.0 x 7.60

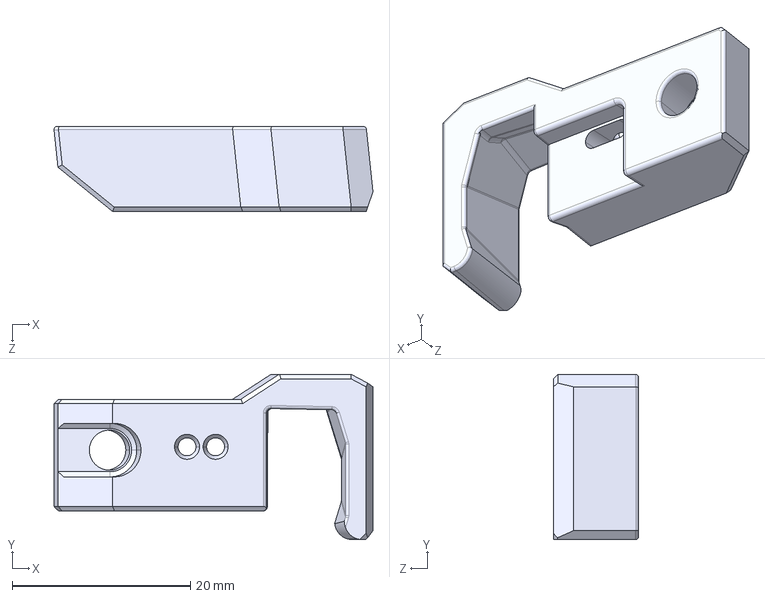
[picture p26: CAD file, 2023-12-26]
EBB SB2240_2209 CAN/CAD/Printed_Part_for_CAN_Cable_V1.2.STEP
35.7 x 18.5 x 9.55 mm

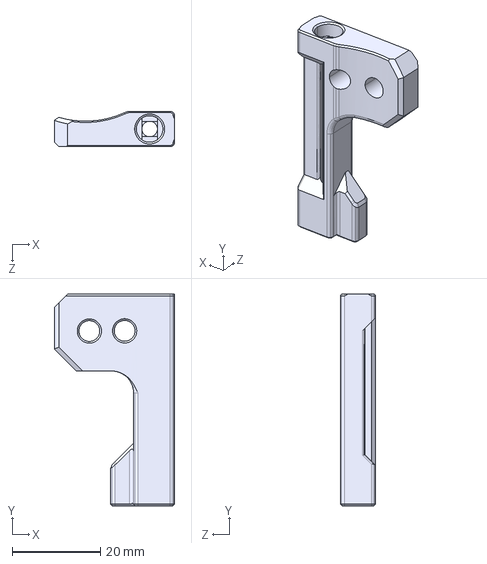
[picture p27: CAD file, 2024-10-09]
EBB_SB2209_USB/CAD/Galileo2_Printable_Files/Beta/Galileo 2 Extruder Chain_Anchor -EBB USB.STEP
27.2 x 48.0 x 8.03 mm

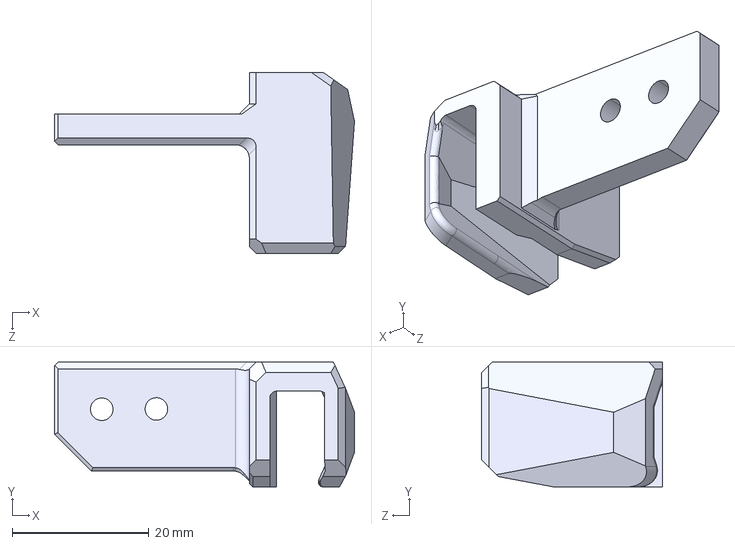
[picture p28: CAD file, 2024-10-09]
EBB_SB2209_USB/CAD/Galileo2_Printable_Files/Beta/Galileo 2 Extruder cable clamp-ebbusb.STEP
43.9 x 18.3 x 26.4 mm

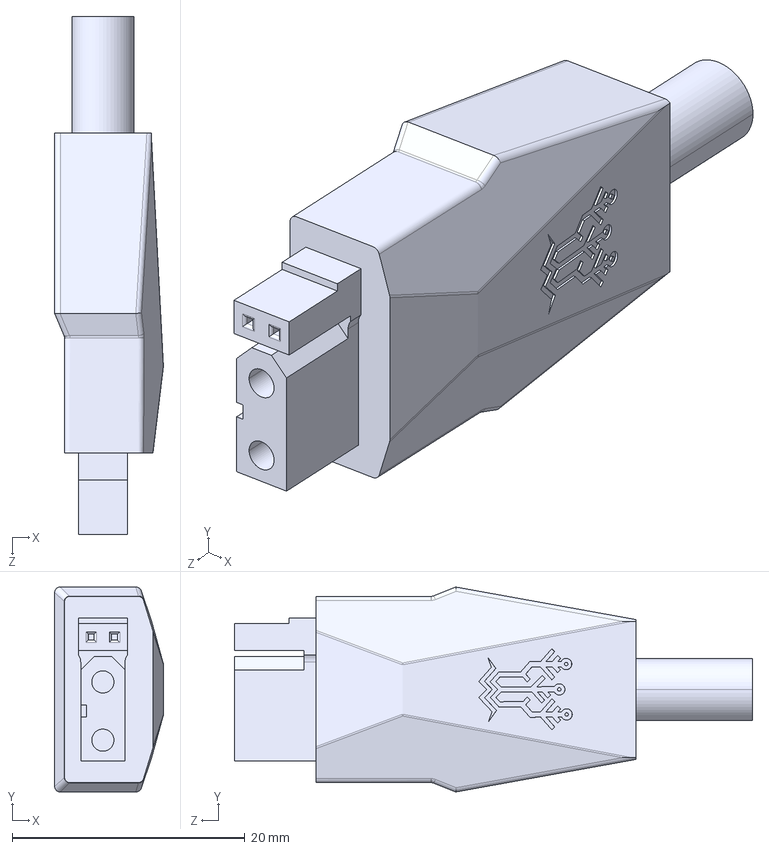
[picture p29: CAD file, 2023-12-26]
EBB SB2240_2209 CAN/CAD/CAN Cable V1.2.STEP
9.35 x 17.6 x 44.5 mm

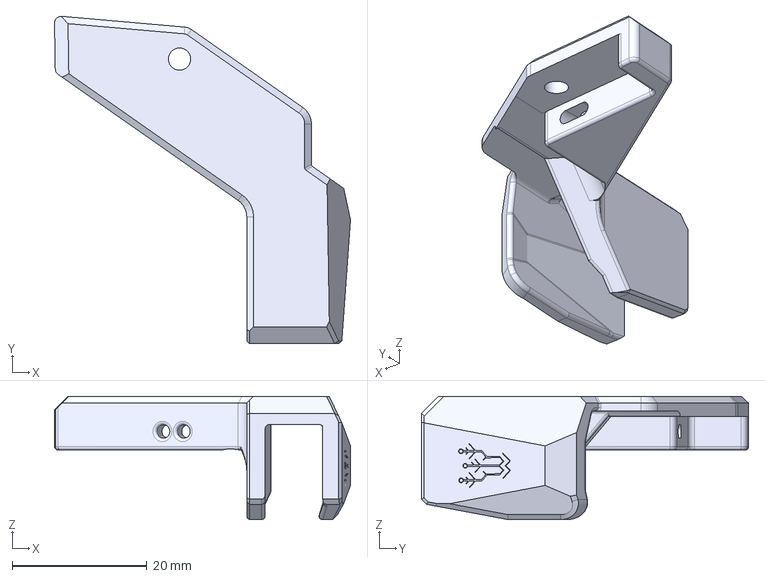
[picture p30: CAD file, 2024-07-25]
EBB_SB2209_USB/CAD/CW2_Printable_Files/Cable_Anchor_EBB-SB-USB.step
43.9 x 48.6 x 18.3 mm

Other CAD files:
EBB SB2240_2209 CAN/CAD/Main_Body_V1.2.STEP
EBB_SB2209_USB/CAD/CW2_Printable_Files/Main_Body_EBB-SB-USB.STEP
EBB_SB2209_USB/STL/CW2_Printable_Files/PCB_Spacer_EBB-SB-USB.STL
EBB_SB2209_USB/CAD/CW2_Printable_Files/Cable_Cover_EBB-SB-USB.STEP
EBB SB2240_2209 CAN/CAD/CW2 Cable Bridge.STEP
EBB SB2240_2209 CAN/CAD/Cable Clip Printed Part.STEP
EBB SB2240_2209 CAN/CAD/Cable_Cover_For_PCB_V1.1.STEP
EBB SB2240_2209 CAN/CAD/Cable_Cover_For_PCB_V1.2.STEP
EBB SB2240_2209 CAN/CAD/Printed Part for USB-C Cable.STEP
EBB SB2240_2209 CAN/STL/CAN Cable V1.2.STL
EBB SB2240_2209 CAN/STL/CW2 Cable Bridge.STL
EBB SB2240_2209 CAN/STL/Cable Clip Printed Part.STL
EBB SB2240_2209 CAN/STL/Cable_Cover_EBB.stl
EBB SB2240_2209 CAN/STL/Cable_Cover_For_PCB_V1.1.STL
EBB SB2240_2209 CAN/STL/Main_Body_EBB.stl
EBB SB2240_2209 CAN/STL/Printed Part for USB-C Cable.STL
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

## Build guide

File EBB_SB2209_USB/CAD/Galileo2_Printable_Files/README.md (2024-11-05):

# EBB USB GALILEO2 PRINTABLE Files

Currently the EBB USB supports the Galileo 2 extruder as a beta set of files. These are available in STEP format within the beta directory under the CAD directory.

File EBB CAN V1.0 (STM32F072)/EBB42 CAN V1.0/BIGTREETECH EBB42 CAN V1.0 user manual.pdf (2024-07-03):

## BIGTREETECH

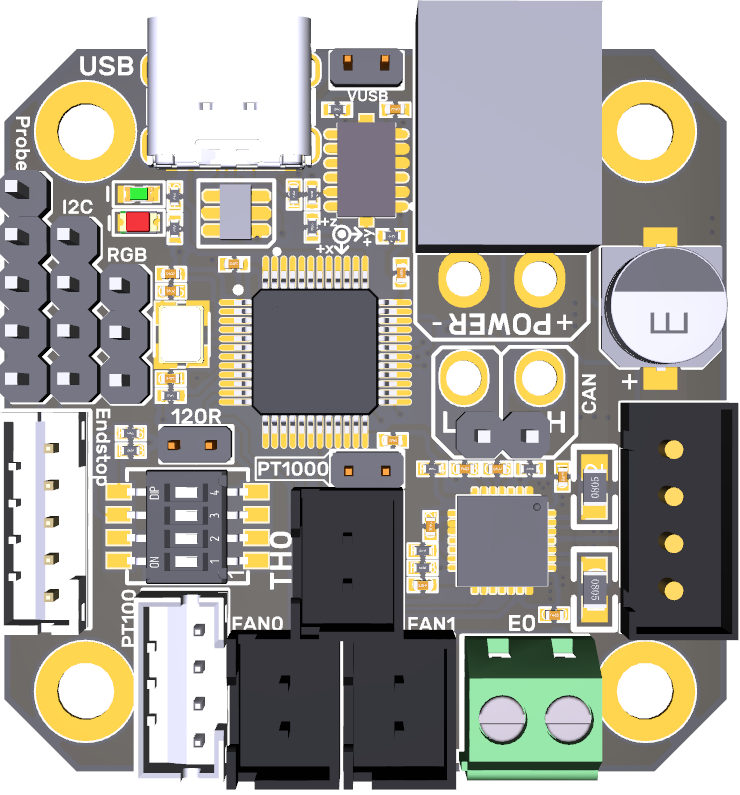
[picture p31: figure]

1 / 19

# BIGTREETECH

# EBB42 CAN V1.0

User Manual

## BIGTREETECH

2 / 19

## Contents

## BIGTREETECH

3 / 19

## Revisions

Version | Statements | Date
01.00 | First Draft | 2022/04/18

## BIGTREETECH

4 / 19

## Ⅰ. Brief Instruction

BIGTREETECH EBB42 CAN V1.0 is a nozzle adapter board specially designed for the 42 extruder stepper motor, which is launched by the 3D printing team Shenzhen Big Tree Technology Co., Ltd. It can communicate via USB port, or CAN BUS, greatly simplifying wirings.

### 1.1 Features

1. With BOOT and RESET buttons reserved, users can update the firmware via DFU mode by USB.
2. Added protection circuit on the thermistor avoids burning the main control chip caused by leakage current from the heating rod.
3. User can select the thermistor's pull-up resistors values through jumper wire, so as to support PT1000 (2.2K pull-up resistors), which makes it convenient for DIY.
4. Connect the USB with a jumper cap to get it power on, which effectively isolates the main control board DC-DC from USB 5V.
5. Reserved I2C interface allows for filament broke and clogged detection, and supports other DIY functions.
6. Added anti-flyback diodes on the heating rod and fans' ports effectively protect the MOS tube from being burned due to reverse voltage.
7. Anti-reverse connection protection on the power interface prevents users from burning the motherboard when mistakenly connecting the reverse power line during DIY.
8. Onboard MAX31865 supports selecting 2-wire or 4-wire of PT100/ PT1000.
9. Supports communication via CAN or USB. The terminal resistor 120R of CAN can be selected through the jumper cap, and it reserves CAN expansion interfaces.
10. Equipped ESD protection chip on the USB port prevents the main control board from being broken down by the static electricity of the USB port.
11. The adaptor board is equipped with terminals, female reeds, double-way studs and screws, which are required accessories for DIY, greatly meeting the DIY needs of customers.

## BIGTREETECH

5 / 19

### 1.2 Parameters

1. External Dimensions: 40mm x 40mm. For further details please read: BIGTREETECH EBB36 CAN V1.0-SIZE.pdf
2. Installation Dimensions: Hole spacing 31mm x 31mm, M3 screw hole x 4
3. Microprocessor: ARM Cortex-M0 STM32F072C8T6 48MHz
4. Input Voltage: DC12V-DC24V 9A
5. Logic Voltage: DC 3.3V
6. Heating Interface: Heating Rod (E0), maximum output current: 5A
7. Onboard Sensor: ADXL345
8. Fan Interfaces: Two CNC Fans (FAN0, FAN1)
9. Maximum Output Current of Fan Interface: 1A, peak value 1.5A
10. Expansion Interfaces: EndStop, I2C, Probe, RGB, PT100/PT1000, USB Interface, CAN Interface
11. Motor Drive: Onboard TMC2209
12. Driver Working Mode: UART
13. Stepper Motor Interface: EM
14. Temperature Sensor Interface(Optional): 1 channel 100K NTC or PT1000 (TH0), 1 channel PT100/PT1000
15. USB Communication Interface: USB-Type-C
16. DCDC 5V Maximum Output Current: 1A

### 1.3 Firmware

BTT EEB42 CAN V1.0 only supports Klipper at the present.

## BIGTREETECH

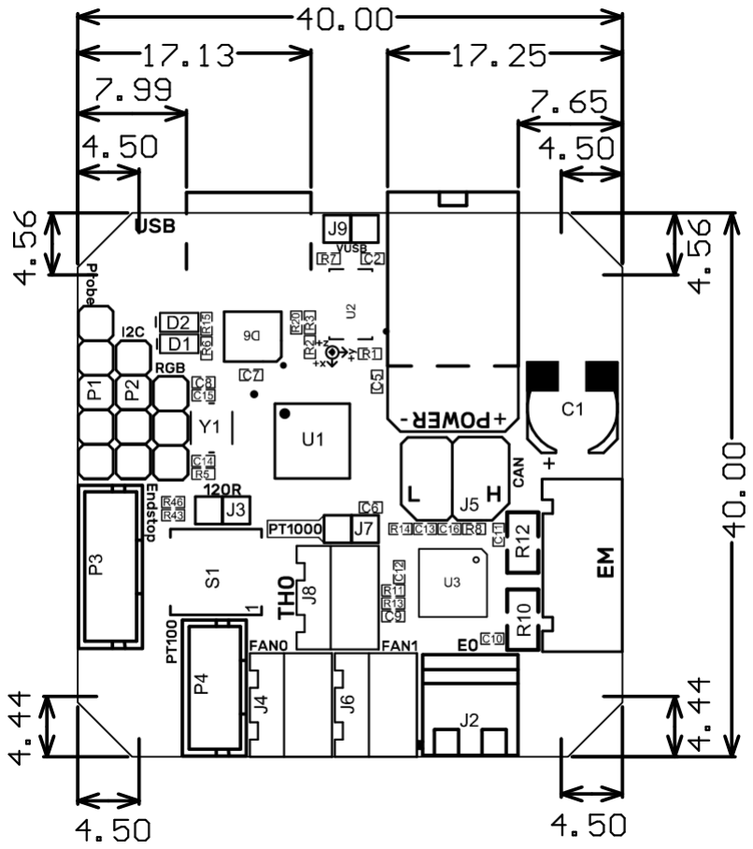
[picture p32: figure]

6 / 19

### 1.4 Size Diagram

## BIGTREETECH

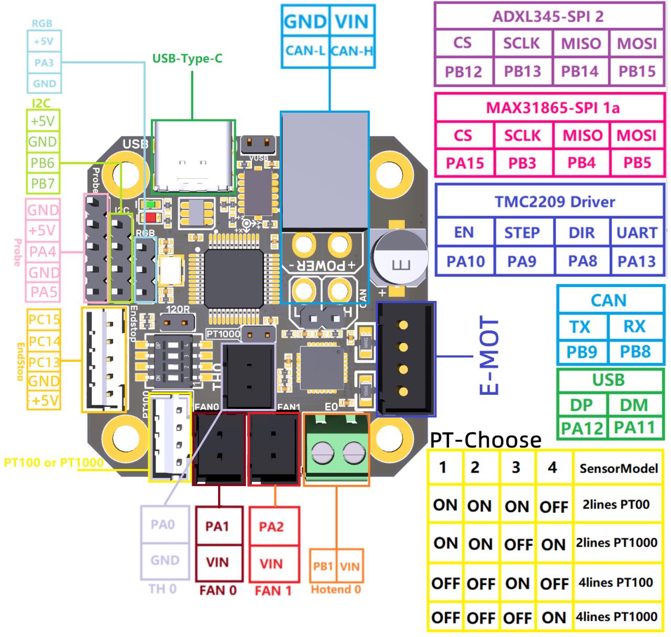
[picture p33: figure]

7 / 19

## II. Peripheral interface

### 2.1 Pin

## BIGTREETECH

8 / 19

## III. Introduction of Interface

### 3.1 USB Power Supply

D1 RGB light will be on when the control board is powers on, which shows supplying normal power. VUSB in the middle of the board is the selection terminal for power. Only when USB supplies power to the board, or the board supplies power through USB, users need to short circuit the VUSB by jump cap.

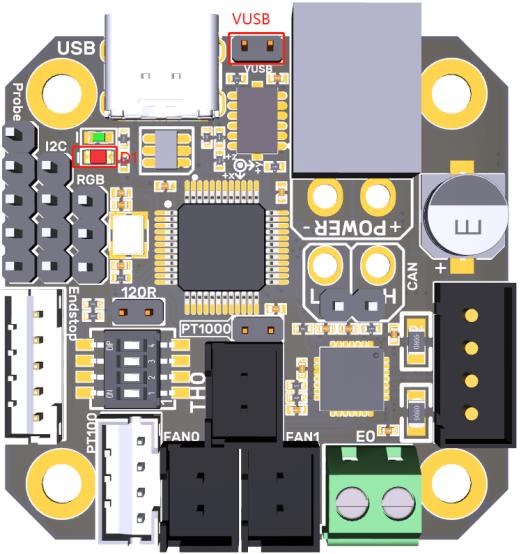
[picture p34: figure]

3.2 100K NTC or PT1000 Settings

1. Version without 31865: No need to insert a jumper cap when using a 100K NTC thermistor, and TH0's pull-up resistor value is 4.7K. When using PT1000, you need to use the jumper cap to short the two pins circled in red as shown below. At this time, TH0's pull-up resistor value is 2.2K (Notice: the temperature accuracy that's read out this way will be less accurate than that of MAX31865).

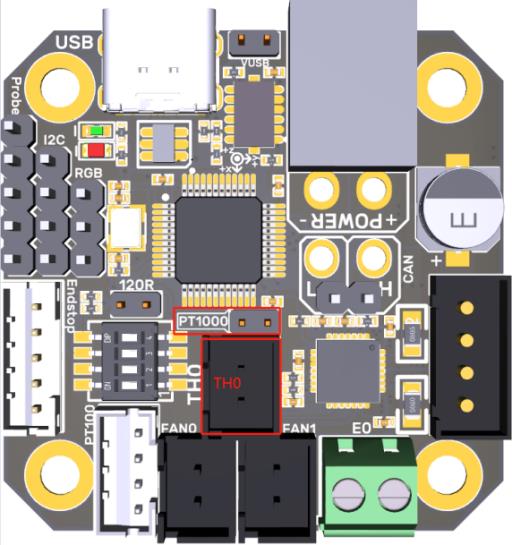
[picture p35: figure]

## BIGTREETECH

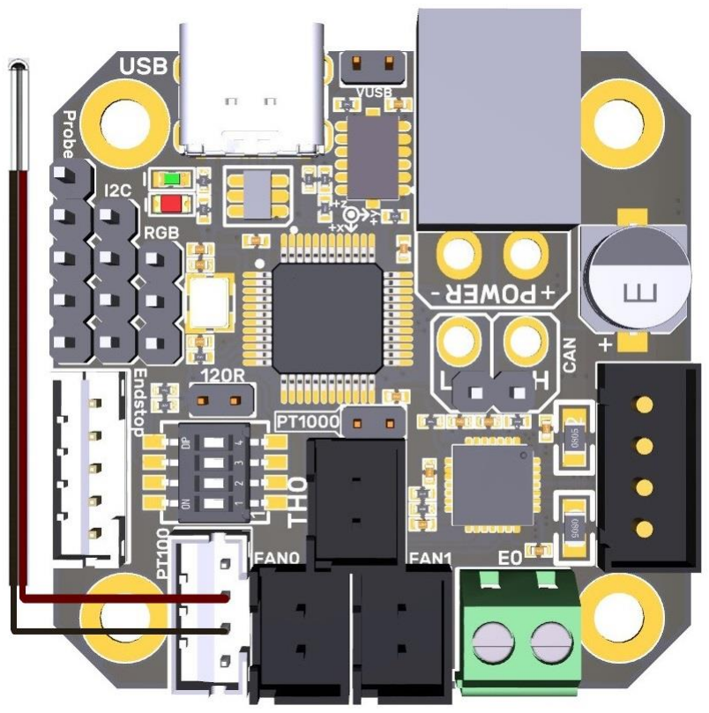
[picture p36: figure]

9 / 19

2. Version with 31865: Select PT100/PT1000 by DIP switch, two-line or four-wire.
1 | 2 | 3 | 4 | Sensor Model
ON | ON | ON | OFF | Two lines PT100
ON | ON | OFF | ON | Two linesPT1000
OFF | OFF | ON | OFF | Four-wire PT100
OFF | OFF | OFF | ON | Four-wire PT1000

## BIGTREETECH

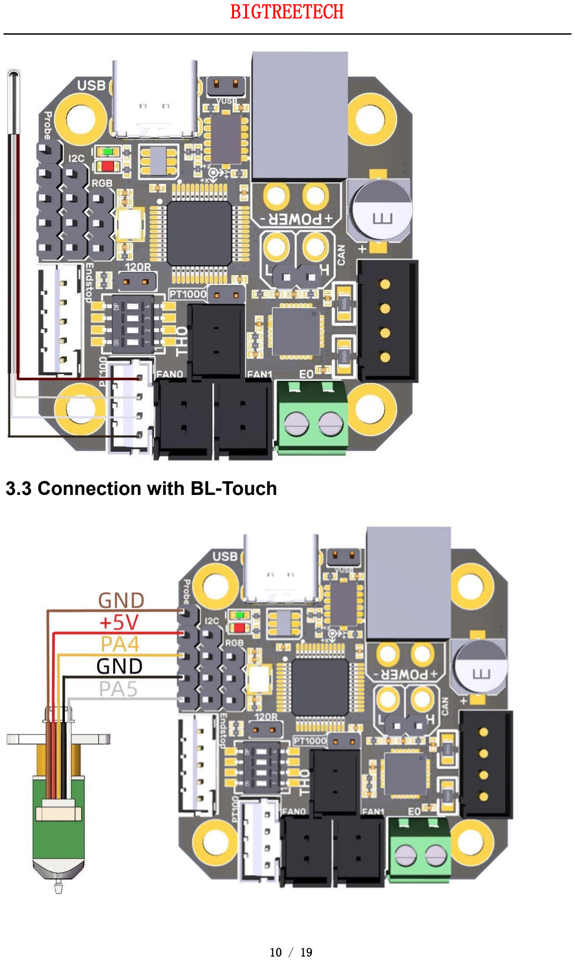
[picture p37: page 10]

10 / 19

### 3.3 Connection with BL-Touch

## BIGTREETECH

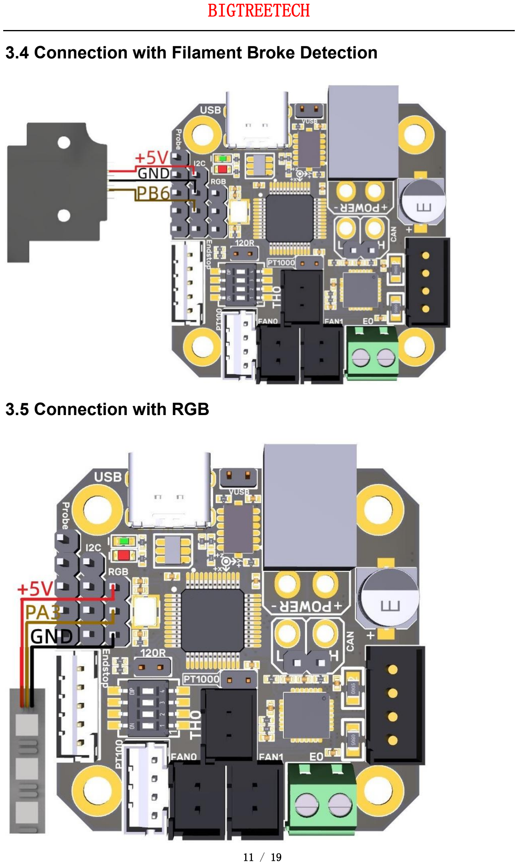
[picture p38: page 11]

11 / 19

### 3.4 Connection with Filament Broke Detection

### 3.5 Connection with RGB

## BIGTREETECH

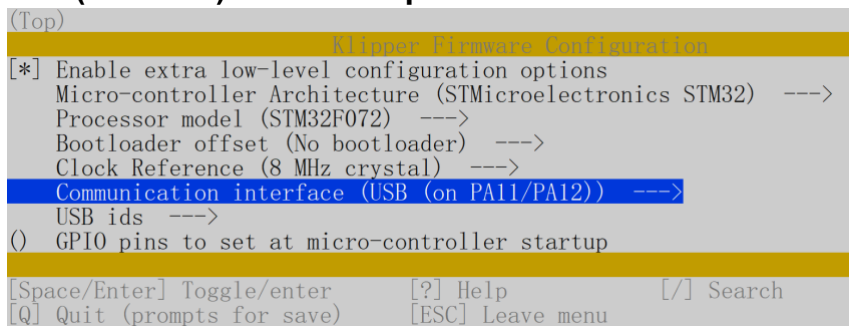
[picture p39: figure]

12 / 19

## IV. Klipper

### 4.1 Compile Firmware

1. After connecting to the Raspberry Pi via ssh, type the below sentences at the command line:
cd ~/klipper/
make menuconfig
Compile the firmware with the following configuration (if the following options are not available, please update the Klipper firmware source to the latest version)

[*] Enable extra low-level configuration options
Micro-controller Architecture (STMicroelectronics STM32) ---> Processor model (STM32F072) --->
Bootloader offset (No bootloader) --->
Clock Reference (8 MHz crystal) --->
If using USB communication over Type-C Communication interface (USB (on PA11/PA12)) ---> If using CANBus communication
Communication interface (CAN bus (on PB8/PB9)) ---> (1000000) CAN bus speed
2. When completed the configuration selection, type 'q' to exit the configuration interface. Select "Yes" when asked whether to save the configuration.
3. Enter make to compile firmware. The 'klipper.bin' firmware that we need will be
generated on the | home/pi/kliiper/out | folder of the Raspberry Pi only once
completed | make. On the left side of ssh software, user can download the
'klipper.bin' firmware directly to the computer.

## BIGTREETECH

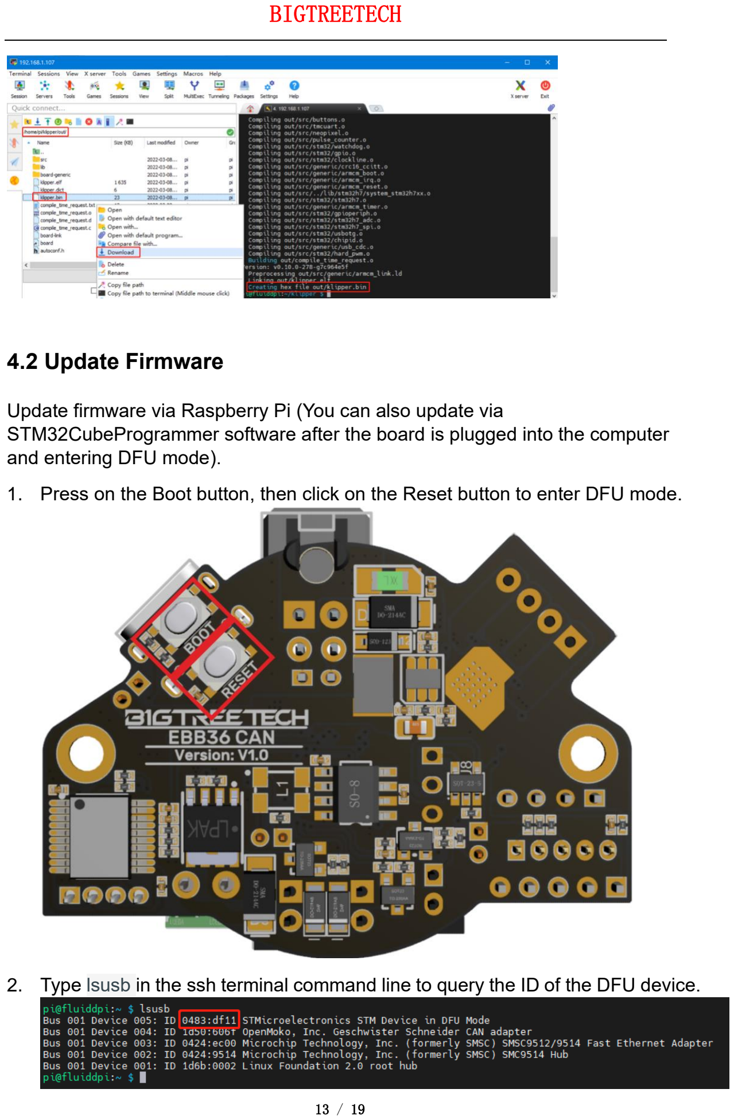
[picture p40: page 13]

13 / 19

### 4.2 Update Firmware

Update firmware via Raspberry Pi (You can also update via STM32CubeProgrammer software after the board is plugged into the computer and entering DFU mode).

1. Press on the Boot button, then click on the Reset button to enter DFU mode.
2. Type lsusb in the ssh terminal command line to query the ID of the DFU device.

## BIGTREETECH

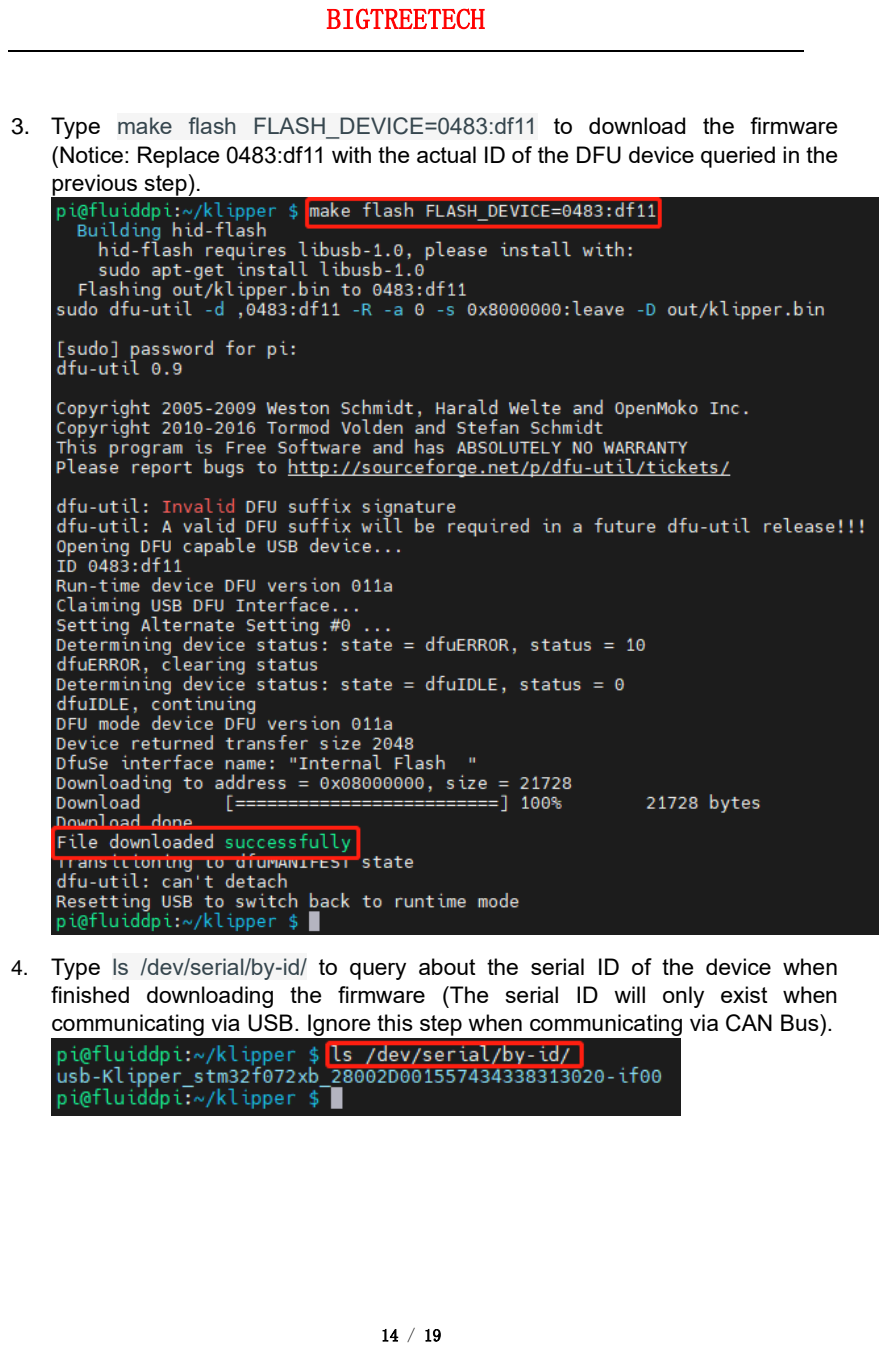
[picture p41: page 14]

14 / 19

3. Type | make flash FLASH_DEVICE=0483:df11 | to download the firmware
(Notice: Replace 0483:df11 with the actual ID of the DFU device queried in the previous step).
4. Type | ls /dev/serial/by-id/ | to query about the serial ID of the device when
finished downloading the firmware (The serial ID will only exist when communicating via USB. Ignore this step when communicating via CAN Bus).

## BIGTREETECH

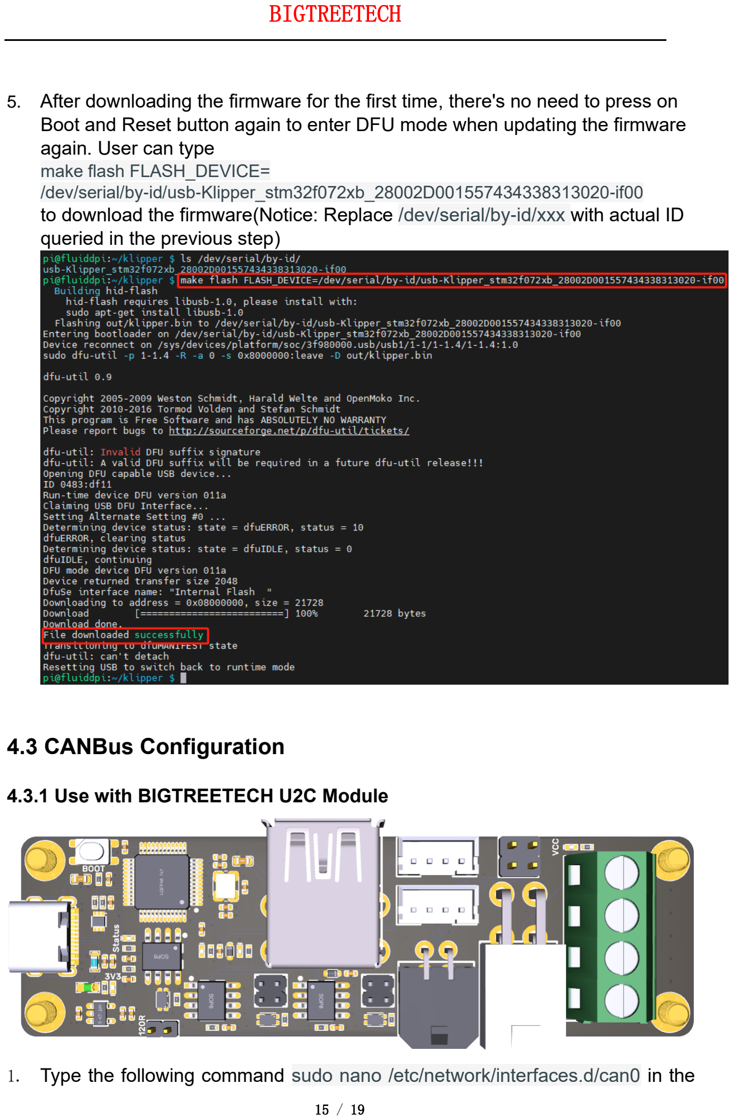
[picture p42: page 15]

15 / 19

5. After downloading the firmware for the first time, there's no need to press on Boot and Reset button again to enter DFU mode when updating the firmware again. User can type
make flash FLASH_DEVICE=
/dev/serial/by-id/usb-Klipper_stm32f072xb_28002D001557434338313020-if00
to download the firmware(Notice: Replace /dev/serial/by-id/xxx with actual ID queried in the previous step)

### 4.3 CANBus Configuration

### 4.3.1 Use with BIGTREETECH U2C Module

1. Type the following command | sudo nano /etc/network/interfaces.d/can0 | in the

## BIGTREETECH

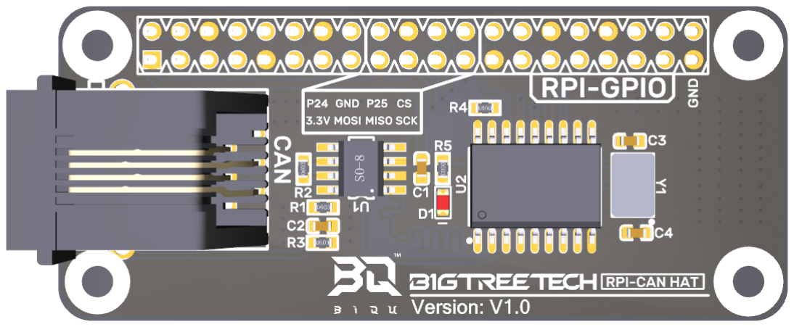
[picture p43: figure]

16 / 19

ssh terminal and execute
auto can0
iface can0 can static
bitrate 1000000
up ifconfig $IFACE txqueuelen 1024
Set the speed for CANBus at 1M(which must be the same as the speed set in the firmware (1000000) CAN bus speed), Save (Ctrl + S) after modification and exit (Ctrl + X).Type command sudo reboot to reboot Raspberry Pi.
2. Every device on CANBus will generate a canbus_uuid based on MCU's ID. If users want to find the ID for every microcontroller, please make sure the hardware is powered on and wired correctly, then run the following command:

~/klippy-env/bin/python ~/klipper/scripts/canbus_query.py can0

3. If detected an uninitialized CAN device, the above command will report the device's canbus_uuid:
Found canbus_uuid=0e0d81e4210c
4. If Klipper operates normally and is connected to the device, then it won't report canbus_uuid, which is normal.

### 4.3.2 Use with BIGTREETECH RPI-CAN HAT Module

1. Type and run the following command sudo nano /boot/config.txt, and added below contents on file config.txt.
dtparam=spi=on
dtoverlay=mcp2515-can0,oscillator=12000000,interrupt=25,spimaxfrequency =1000000
After modification, save(Ctrl + S)and exist(Ctrl + X), type sudo reboot to reboot Raspberry Pi.
2. Type and run commands | dmesg | grep -i '\(can\|spi\)' | to test if RPI-CAN HAT

## BIGTREETECH

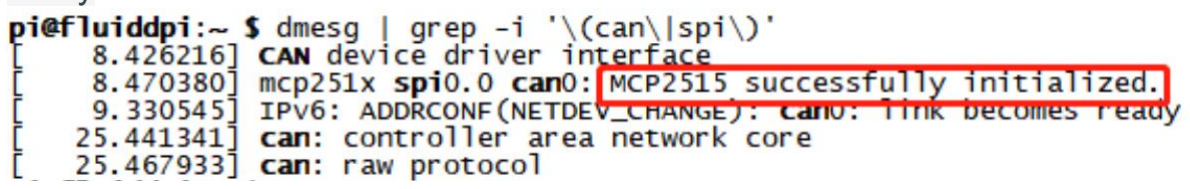
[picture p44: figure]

17 / 19

module is normally connected. The normal response should be as below:
[ 8.680446] CAN device driver interface
[ 8.697558] mcp251x spi0.0 can0: MCP2515 successfully initialized.
[ 9.482332] IPv6: ADDRCONF(NETDEV_CHANGE): can0: link becomes ready
3. Type sudo nano /etc/network/interfaces.d/can0 on the ssh terminal and run the command.
auto can0
iface can0 can static
bitrate 1000000
up ifconfig $IFACE txqueuelen 1024
Set the speed for CANBus at 1M(which must be the same as the speed set in the firmware (1000000) CAN bus speed). Save (Ctrl + S) after modification and exit (Ctrl + X). Type command sudo reboot to reboot Raspberry Pi.
4. Every device on CANBus will generate a canbus_uuid base on MCU's ID. If users want to find ID for every microcontroller, please make sure the hardware is powered on and wired correctly, then run the following command: ~/klippy-env/bin/python ~/klipper/scripts/canbus_query.py can0
5. If detected an uninitialized CAN device, the above command will report the device's canbus_uuid:
Found canbus_uuid=0e0d81e4210c
6. If Klipper operates normally and is connected to the device, then it won't report the canbus_uuidm, which is normal.

## BIGTREETECH

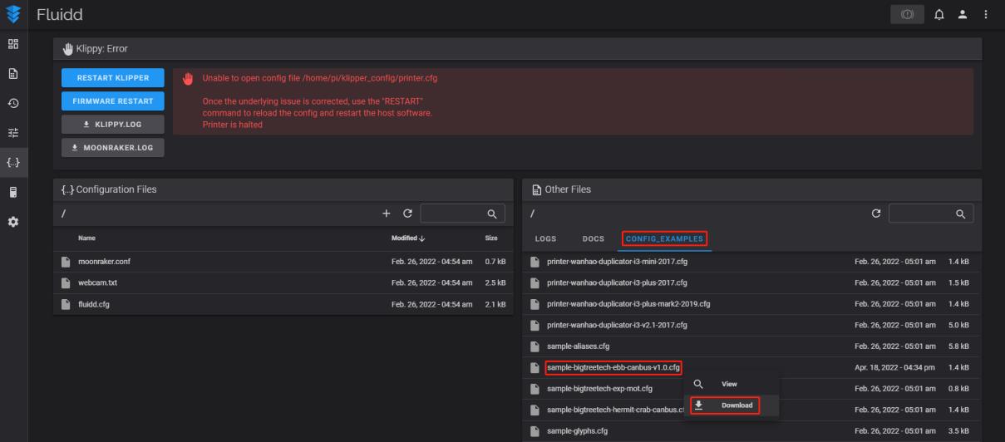
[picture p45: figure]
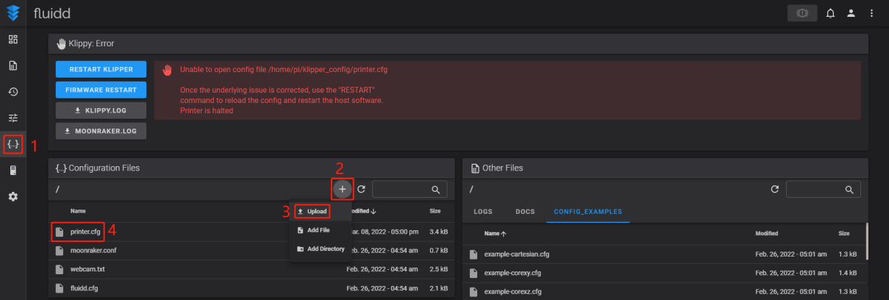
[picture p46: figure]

18 / 19

### 4.4 Klipper Configuration

1. Enter Raspberry Pi's IP address in a browser to access the page as shown below picture, and download the reference configuration of the motherboard. If you cannot find this file, please update the Klipper firmware source code to the latest version, or download it from github https://github.com/bigtreetech/EBB (https://github.com/bigtreetech/SKR-3)
2. Upload the board's configuration files to the Configuration files as shown below.
3. Add the board's configuration to the file“printer.cfg". [include sample-bigtreetech-ebb-canbus-v1.0.cfg]
4. Revise the ID number of the configuration files as the actual ID of the board ( Via USB serial or CANBus).
5. Configure the specific functions of modules as instructed below:

## BIGTREETECH

19 / 19

https://www.klipper3d.org/Overview.html

## V. Cautions

1. When the TH0 interface doesn't use PT1000, you can't insert the jump cap on it, otherwise 100K NTC won't be used as normal.
2. When using CAN communication, you need to see whether it is used as a terminal. If it is, you must insert the jumper cap on the 120R position.
3. When DIY crimping, you need to pay attention to the line sequences, and do DIY according to the Pin diagram so as to avoid the power line from being reversely connected or connected to the CAN signal, which will get the module burned.
4. If there's no external power supply during writing firmware via USB port, you need to short the VUSB by jumper cap so as to supply the module with working voltage.
5. The load current of the heating rod and the fan interfaces shall not exceed the maximum withstand current to prevent the MOS tube from being burned out.

## VI. FAQ

Q: What's the maximum current for the heating rod and fan interface? A: The maximum output current of the heating rod port: 5A.

The maximum output current of the fan interface: 1A, peak value 1.5A.

The total current for the heating rod, stepper driver and fans needs to be less than 9A.

Q: Cannot update firmware via USB port?
A: You need to make sure that the jump cap is inserted on VUSB, and the indicator light on the board is on.

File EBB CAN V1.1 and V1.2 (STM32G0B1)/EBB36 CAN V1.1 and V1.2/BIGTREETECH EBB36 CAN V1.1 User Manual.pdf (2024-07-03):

## BIGTREETECH

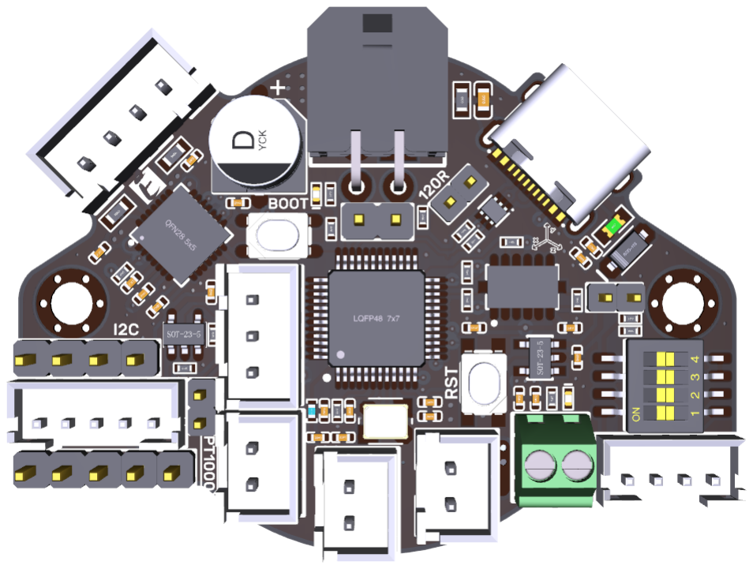
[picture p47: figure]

1 / 21

# BIGTREETECH EBB36 CAN V1.1

# User Manual

## BIGTREETECH

2 / 21

## Contents

## BIGTREETECH

3 / 21

## Revision History

Revision | Description | Date
01.00 | First Draft | 2022/05/16
01.01 | Correct the wrong mark of the heater cartridge port on the pin diagram. | 2022/05/21
01.02 | CAN bus recommendation speed increased from 250K to 1M | 2024/07/02

## BIGTREETECH

4 / 21

## 1 Product Introduction

BIGTREETECH EBB36 CAN V1.1 is a nozzle adapter board made by the 3D printing team of Shenzhen BIQU Technology Co., Ltd. for a 36 stepper motor extruder. It can communicate via a USB or CAN, which greatly simplifies wiring.

### 1.1 Product Features

1. With a BOOT and RESET buttons reserved, users can update the firmware via DFU mode by USB.
2. Adding a protection circuit on the thermistor avoids burning the main control chip caused by electric leakage of the heater cartridge.
3. The thermistor can select the pull-up resistor value via a jumper, in this way, it can support PT1000 (2.2K pull-up resistor), which is convenient for DIY.
4. The USB power is selected through a jumper cap, which effectively isolates the motherboard DC-DC and USB 5V.
5. Reserve the I2C interface, this interface can also be used for filament runout/blocking detection, or DIY for other functions.
6. A follow current diodes are added to the inductive load interface (fan) to ensure that when the fan MOS is turned off, the fan winding current has a follow current loop, which effectively prevents the high voltage generated by the winding drain at the MOS tube when it is turned off. Considering the size of the board and the switch characteristics of the extruder fan, a Schottky diode in a SOD-323 package is used.
7. The DCDC step-down circuit is reversely connected to a diode to prevent the subsequent circuit from being damaged due to the reverse connection of the power line.
8. Onboard MAX31865 (optional function, the version without 31865 does not have this function, but there are reserved pads), supports 2-wire/4-wire PT100/PT1000 selection.
9. Support communication via CAN or USB. The terminal resistor 120R of CAN can be selected through a jumper cap, and it reserves a CAN expansion interface.
10. Equipping the ESD protection chip on the USB port prevents the main control from being broken down by the static electricity of the USB port.
11. Limit switch hardware debouncing circuit.

## BIGTREETECH

5 / 21

12. The adaptor board is equipped with terminals, female reeds, double-way studs and screws, which are required for DIY, greatly meeting the DIY needs of customers.
13. Support CAN bus connection, which has long data transmission, strong anti-noise ability, strong real-time performance and high reliability.

### 1.2 Product Parameters

1. Product Size: 51.5 x 37mm, for further details please read: BIGTREETECH EBB36 CAN V1.1-SIZE.pdf
2. Installation Dimensions: Hole Spacing 43.85mm, M3 Screw Hole x 2
3. Microprocessor: ARM Cortex-M0+ STM32G0B1CBT6 64MHz
4. Input Voltage: DC12V-DC24V 6A
5. Logic Voltage: DC 3.3V
6. Heating Interface: Heater Cartridge (E0), maximum output current: 5A
7. Onboard Sensor: ADXL345
8. Fan Interfaces: Two CNC Fans (FAN0, FAN1)
9. Maximum Output Current of Fan Interface: 1A
10. Expansion Interfaces: EndStop, I2C, Probe, RGB, PT100/PT1000, USB Interface, CAN Interface
11. Motor Drive: Onboard TMC2209, Hardware Address: 00, Rsense: 0.11R
12. Driver Working Mode: UART
13. Stepper Motor Interface: E
14. Temperature Sensor Interface Optional: One for 100K NTC or PT1000(TH0), one for PT100/PT1000
15. USB Communication Interface: USB-Type-C
16. DC-DC 5V Maximum Output Current: 1A

### 1.3 Firmware Support

This product currently only supports Klipper.

## BIGTREETECH

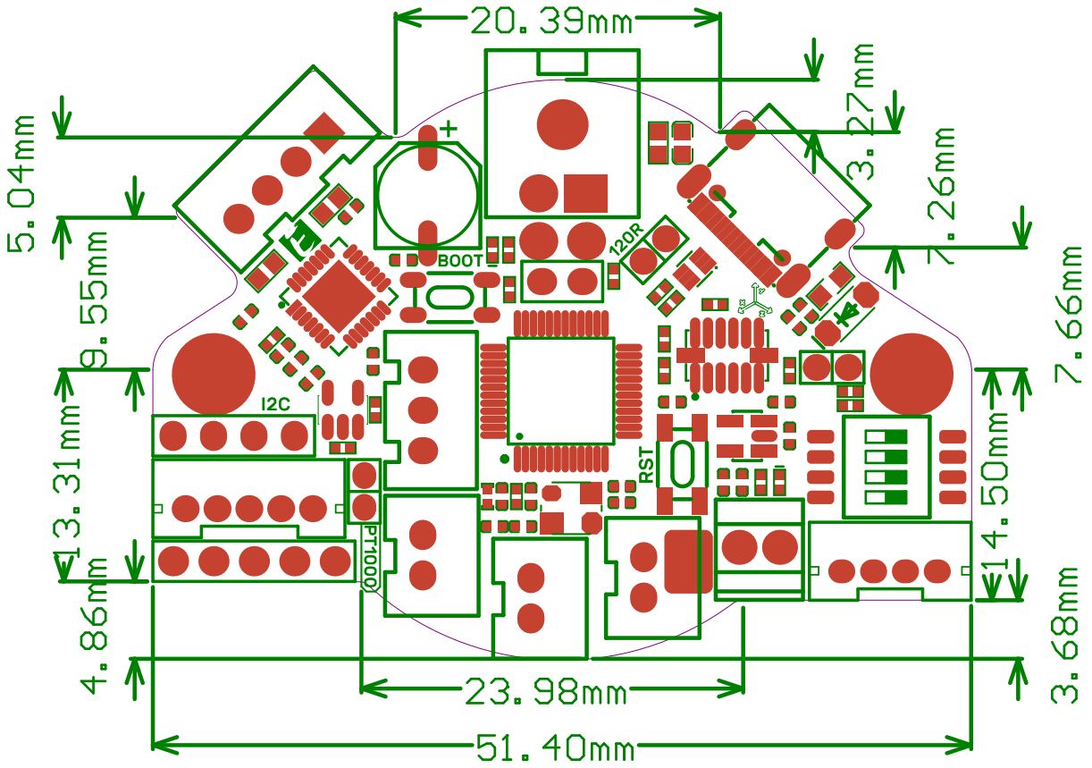
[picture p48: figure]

6 / 21

### 1.4 Product Size

## BIGTREETECH

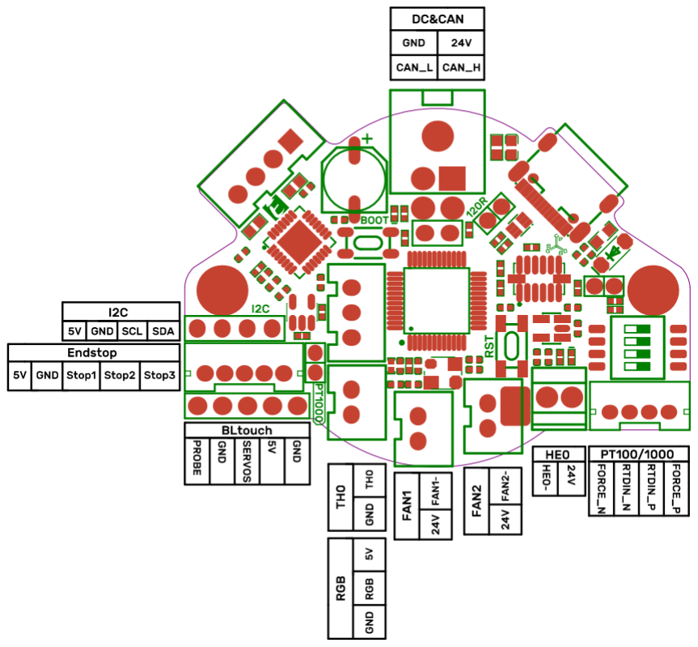
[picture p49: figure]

7 / 21

## 2 Peripheral Interface

### 2.1 Pin Instruction

## 3 Introduction of Interface

### 3.1 USB Power Supply

After the motherboard is powered on, the yellow-green LED1 lights will light up, indicating a normal power supply. The VUSB on the right side of the board is the power selection terminal. Only when using USB to supply power to the motherboard or need to supply power through USB, do you need to use the

## BIGTREETECH

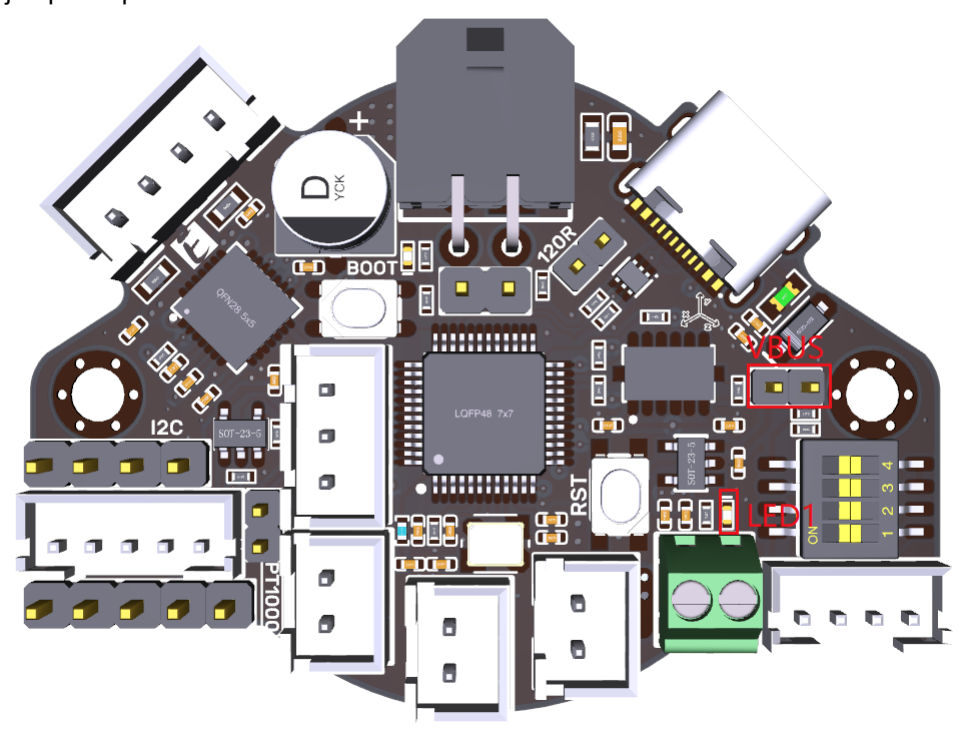
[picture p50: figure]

8 / 21

jumper cap to connect VUSB.

## BIGTREETECH

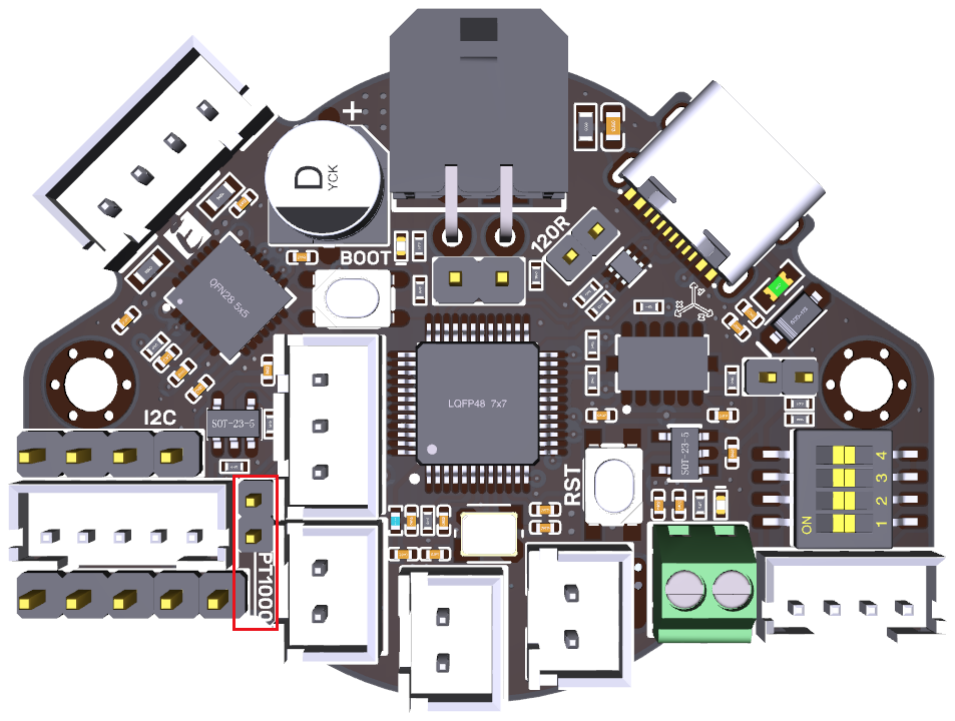
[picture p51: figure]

9 / 21

3.2 100K NTC or PT1000 Settings

1. Version without 31865: No need to plug a jumper cap when using a 100K NTC thermistor, and TH0's pull-up resistor value is 4.7K. When using PT1000, you need to use the jumper cap to short the two pins, as shown below picture. At this time, TH0's pull-up resistor value is 2.2K (Notice: the temperature accuracy that's read out this way will be less accurate than that of MAX31865).
2. Version with 31865: Select PT100/PT1000 by DIP switch, two-line or four-wire:
1 | 2 | 3 | 4 | Sensor Model
ON | ON | ON | OFF | Two lines PT100
ON | ON | OFF | ON | Two lines PT1000
OFF | OFF | ON | OFF | Four-wire PT100
OFF | OFF | OFF | ON | Four-wire PT1000

## BIGTREETECH

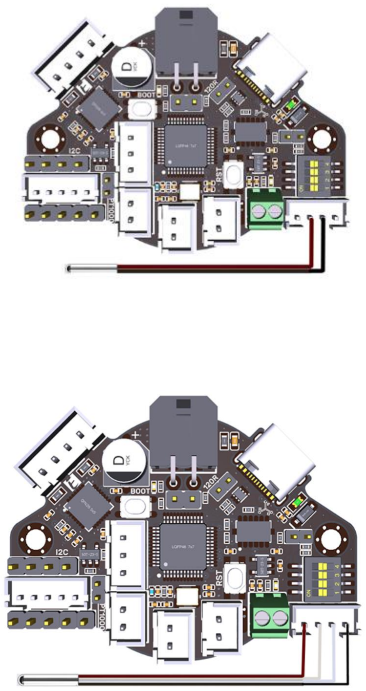
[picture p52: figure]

10 / 21

## BIGTREETECH

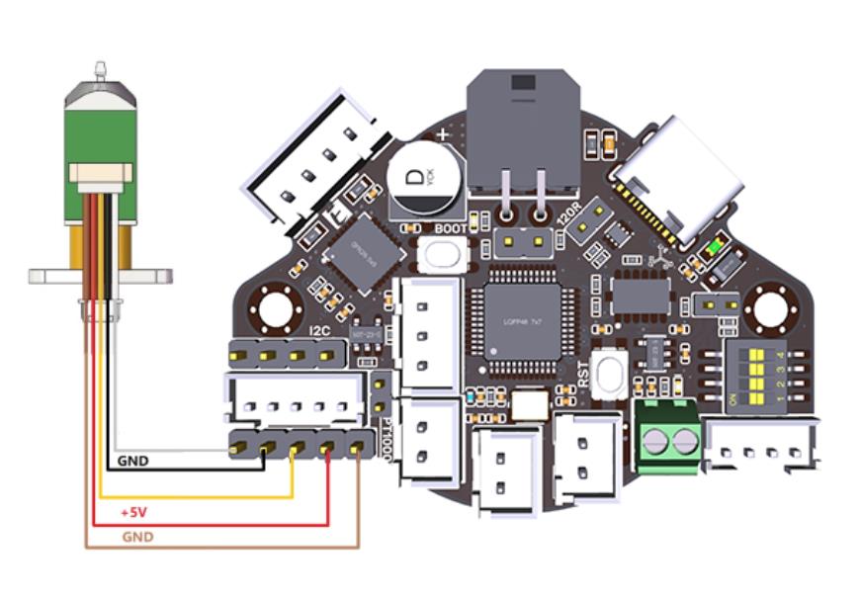
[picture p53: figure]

11 / 21

### 3.3 BL-Touch Wiring

## BIGTREETECH

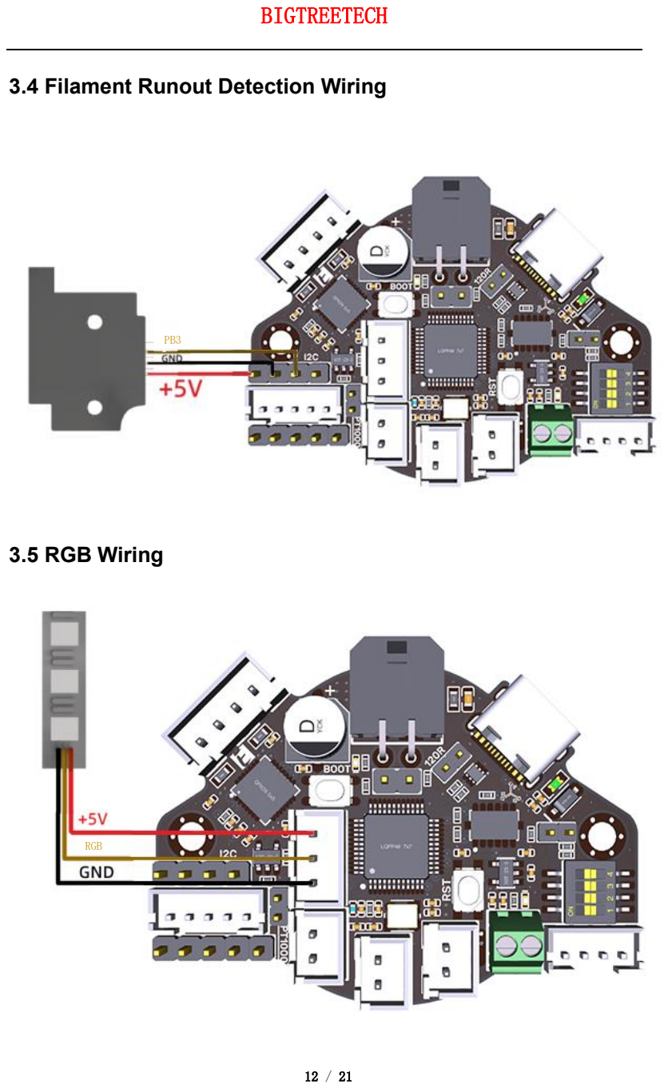
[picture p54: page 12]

12 / 21

### 3.4 Filament Runout Detection Wiring

### 3.5 RGB Wiring

PB3

RGB

## BIGTREETECH

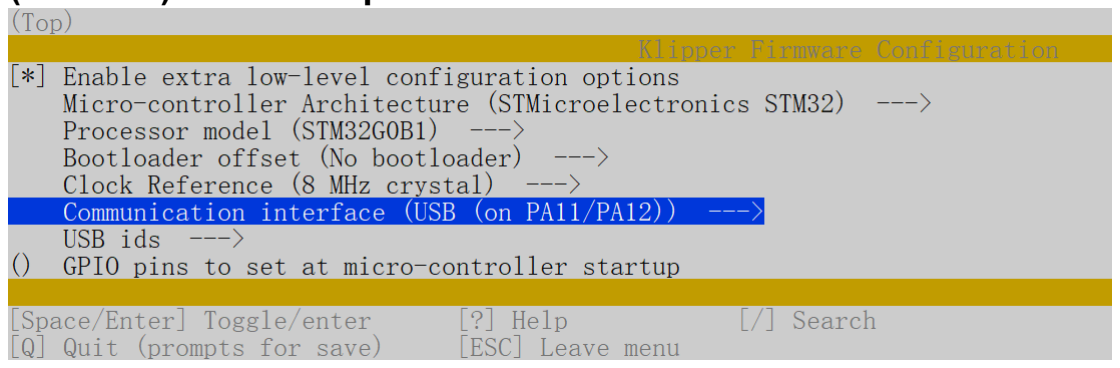
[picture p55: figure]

13 / 21

## 4 Klipper

### 4.1 Firmware Compilation

1. After connecting to the Raspberry Pi via SSH, type the below sentences at the command line:
cd ~/klipper/
make menuconfig
Compile the firmware with the following configuration (if the following options are not available, please update the Klipper source to the latest version). [*] Enable extra low-level configuration options
Micro-controller Architecture (STMicroelectronics STM32) ---> Processor model (STM32G0B1) --->
Bootloader offset (No bootloader) --->
Clock Reference (8 MHz crystal) --->
If using USB communication over Type-C Communication interface (USB (on PA11/PA12)) ---> If using CANBus communication
Communication interface (CAN bus (on PB0/PB1)) ---> (1000000) CAN bus speed
2. When the configuration is completed, type 'q' to exit the configuration interface. Select "Yes" when asked whether to save the configuration.
3. Enter make to compile the firmware. The 'klipper.bin' firmware that we need will be generated on the home/pi/klipper/out folder of the Raspberry Pi when completed. The firmware is on the left side of SSH software, users can download it directly to the computer.

## BIGTREETECH

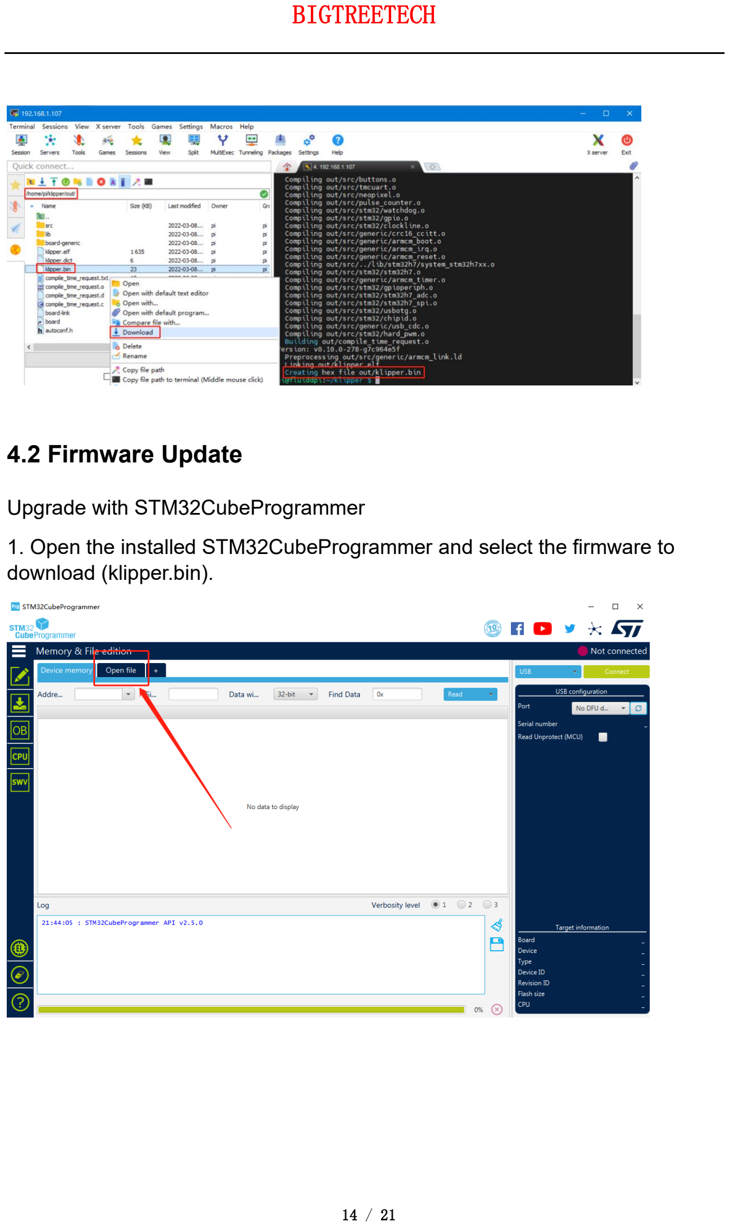
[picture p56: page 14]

14 / 21

### 4.2 Firmware Update

Upgrade with STM32CubeProgrammer

1. Open the installed STM32CubeProgrammer and select the firmware to download (klipper.bin).

## BIGTREETECH

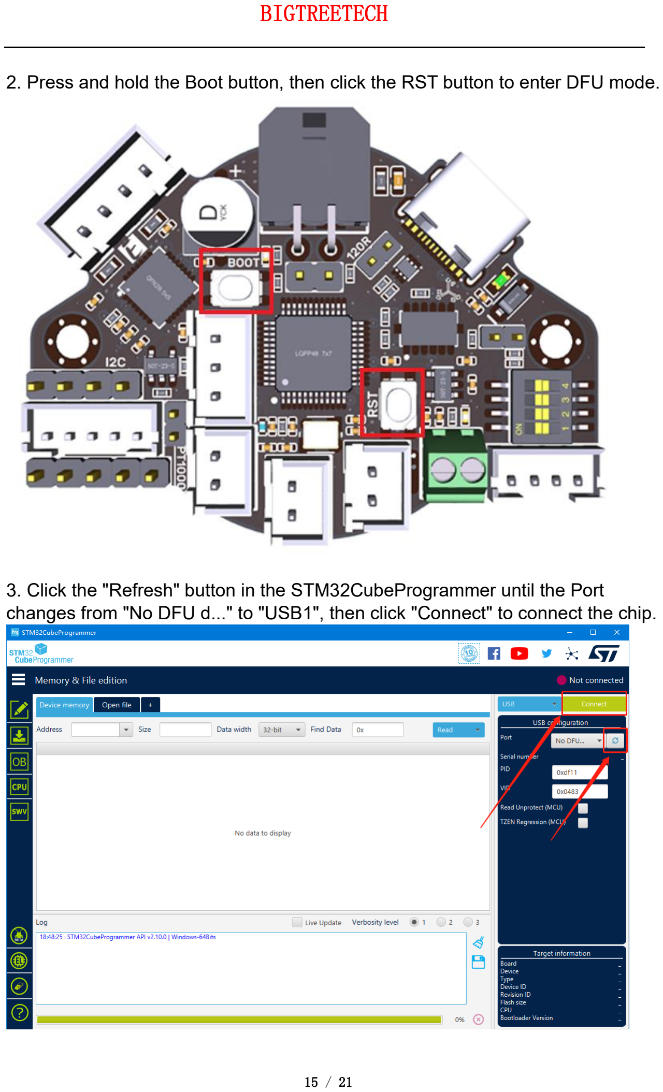
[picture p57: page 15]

15 / 21

2. Press and hold the Boot button, then click the RST button to enter DFU mode.
3. Click the "Refresh" button in the STM32CubeProgrammer until the Port changes from "No DFU d..." to "USB1", then click "Connect" to connect the chip.

## BIGTREETECH

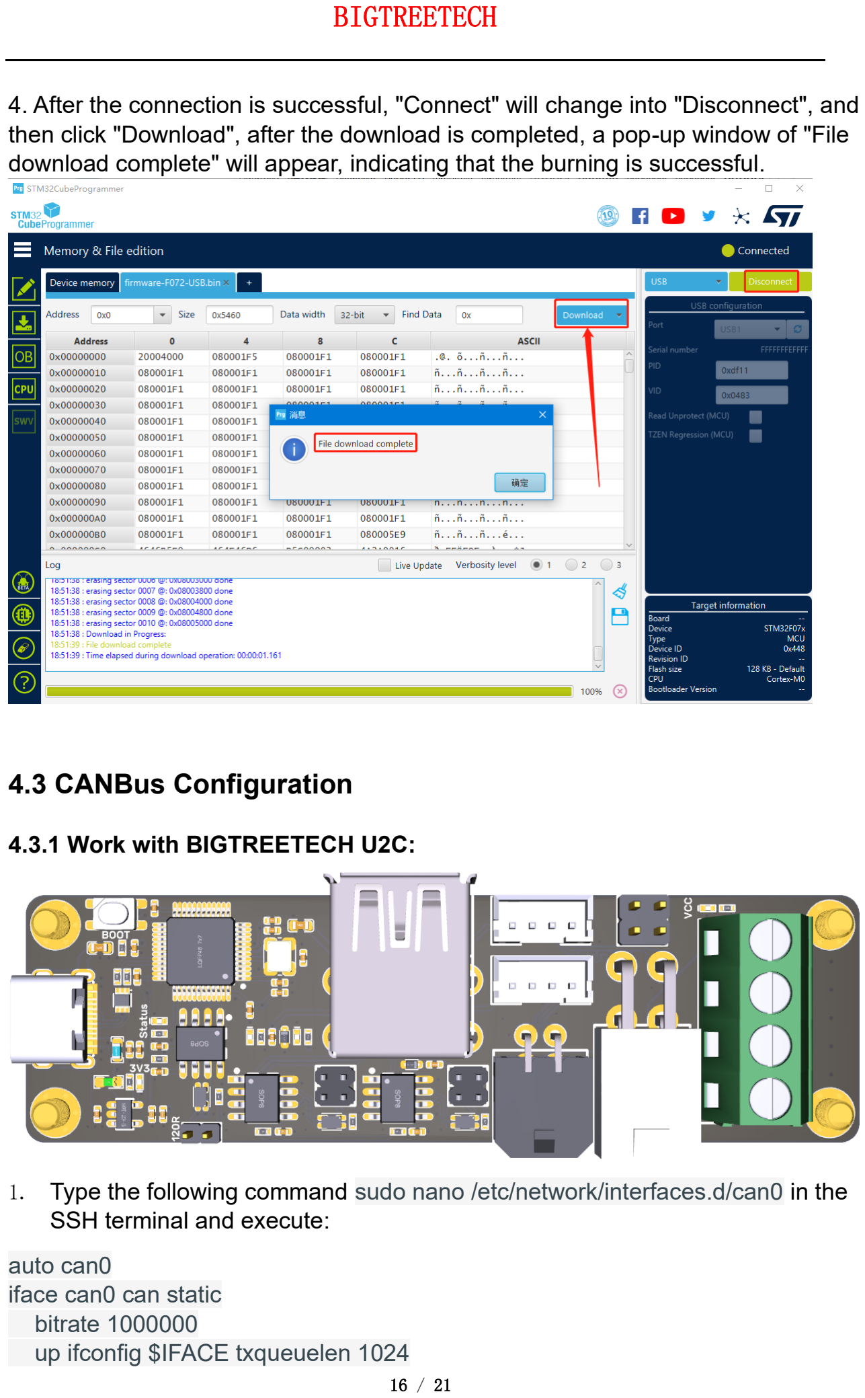
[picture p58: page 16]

16 / 21

4. After the connection is successful, "Connect" will change into "Disconnect", and then click "Download", after the download is completed, a pop-up window of "File download complete" will appear, indicating that the burning is successful.

### 4.3 CANBus Configuration

### 4.3.1 Work with BIGTREETECH U2C:

1. Type the following command | sudo nano /etc/network/interfaces.d/can0 | in the
SSH terminal and execute:

auto can0
iface can0 can static
bitrate 1000000
up ifconfig $IFACE txqueuelen 1024

## BIGTREETECH


17 / 21

Set the speed for CANBus at 1M(must be the same as the speed set in the
firmware | (1000000) CAN bus speed), Save(Ctrl + S)after modification and
exit(Ctrl + X), Type | | sudo rebootto to reboot Raspberry Pi.
2. Every device on CANBus will generate a canbus_uuid based on MCU's UID. If users want to find the ID for every microcontroller, please make sure the hardware is powered on and wired correctly, then run the following command: ~/klippy-env/bin/python ~/klipper/scripts/canbus_query.py can0
3. If detected an uninitialized CAN device, the above command will report the device's canbus_uuid:
Found canbus_uuid=0e0d81e4210c
4. If Klipper operates normally and is connected to the device, then it won’t report canbus_uuid, which is also normal.

### 4.3.2 Work with BIGTREETECH RPI-CAN HAT:

1. Type and run the following command sudo nano /boot/config.txt, and added below contents on file config.txt.
dtparam=spi=on
dtoverlay=mcp2515-
can0,oscillator=12000000,interrupt=25,spimaxfrequency=1000000
After modification, save(Ctrl + S)and exist(Ctrl + X), type | sudo reboot | to
reboot Raspberry Pi.
2. Type and run commands dmesg | grep -i '\(can\|spi\)' to test if RPI-CAN HAT
module is normally connected. The normal response should be as below:

[ 8.680446] CAN device driver interface
[ 8.697558] mcp251x spi0.0 can0: MCP2515 successfully initialized.
[ 9.482332] IPv6: ADDRCONF(NETDEV_CHANGE): can0: link becomes ready

## BIGTREETECH

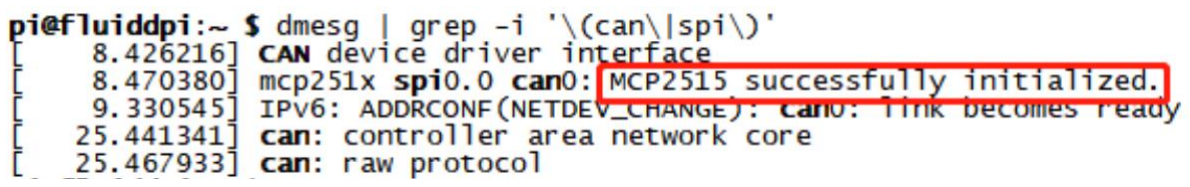
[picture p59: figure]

18 / 21

3. Type | sudo nano /etc/network/interfaces.d/can0 | on the SSH terminal and run
the command.
auto can0
iface can0 can static
bitrate 1000000
up ifconfig $IFACE txqueuelen 1024
Set the speed for CANBus at 1M(must be the same as the speed set in the firmware (1000000) CAN bus speed). Save (Ctrl + S) after modification and
exit (Ctrl + X). Type command | sudo reboot | to reboot Raspberry Pi.
4. Every device on CANBus will generate a canbus_uuid base on MCU's UID. If users want to find the ID for every microcontroller, please make sure the hardware is powered on and wired correctly, then run the following command: ~/klippy-env/bin/python ~/klipper/scripts/canbus_query.py can0
5. If detected an uninitialized CAN device, the above command will report the device's canbus_uuid:
Found canbus_uuid=0e0d81e4210c
6. If Klipper operates well and is connected to the device, then it won't report the canbus_uuid, which is normal.

## BIGTREETECH

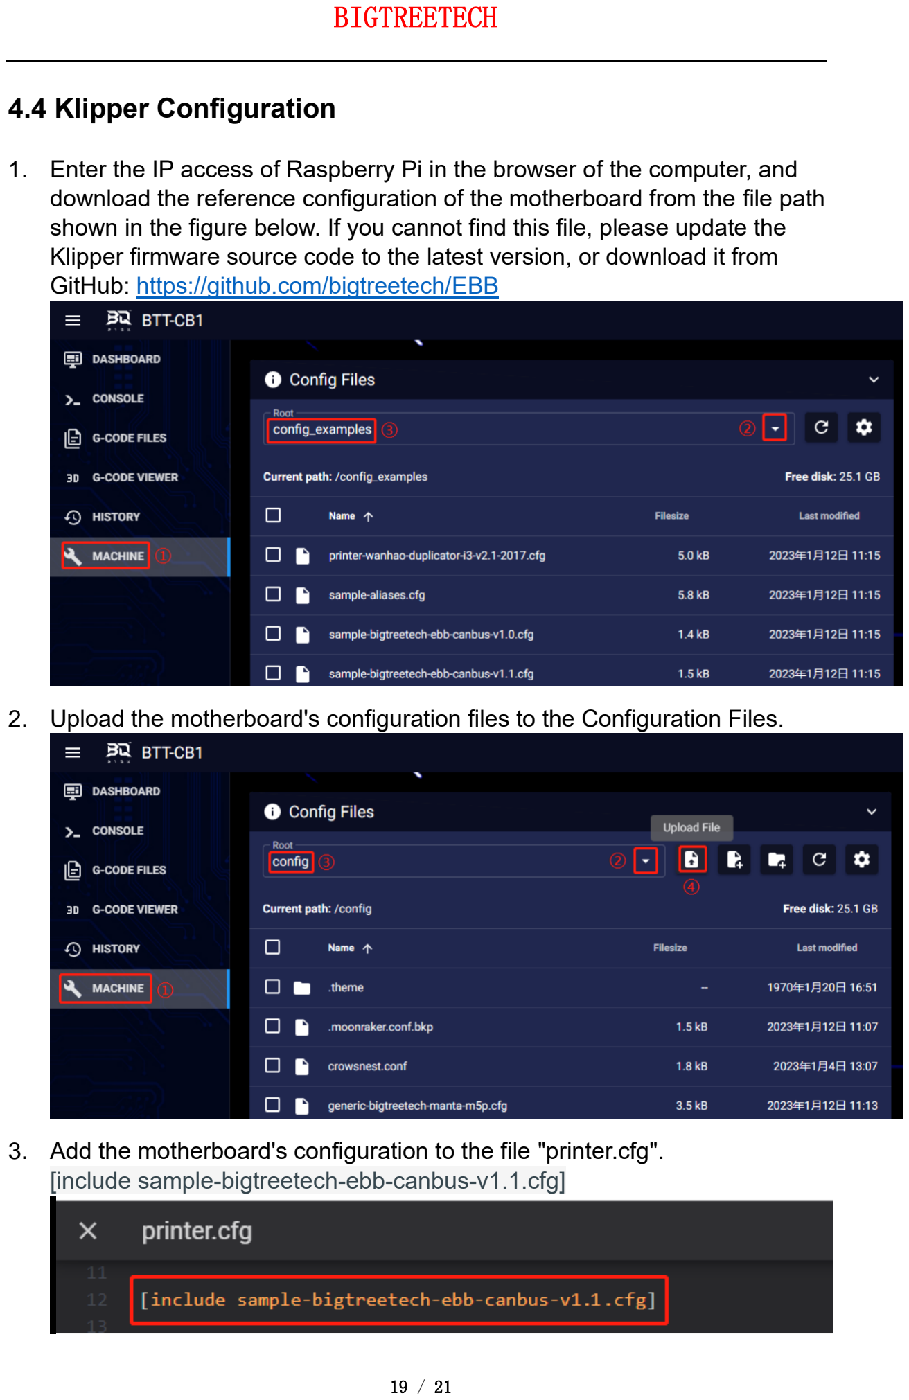
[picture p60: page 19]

19 / 21

### 4.4 Klipper Configuration

1. Enter the IP access of Raspberry Pi in the browser of the computer, and download the reference configuration of the motherboard from the file path shown in the figure below. If you cannot find this file, please update the Klipper firmware source code to the latest version, or download it from GitHub: https://github.com/bigtreetech/EBB (https://github.com/bigtreetech/SKR-3)
2. Upload the motherboard's configuration files to the Configuration Files.
3. Add the motherboard's configuration to the file "printer.cfg". [include sample-bigtreetech-ebb-canbus-v1.1.cfg]

## BIGTREETECH

20 / 21

4. Revise the ID number of the configuration files as the actual ID of the motherboard (USB serial or CANBus).
5. Configure the specific functions of the module as instructed below:

https://www.klipper3d.org/Overview.html

## 5 Cautions

1. When the TH0 interface doesn't work with PT1000, you can't plug a jump cap on it, otherwise 100K NTC won't work as normal.
2. When using CAN communication, you need to see whether it is used as a terminal. If it is, you must plug a jumper cap on the 120R position.
3. When DIY crimping, wire according to the silkscreen, and DIY according to the Pin and Schematic diagrams so as to avoid the power line from being reversely connected or connected to the CAN signal, which will get the module burned.
4. If there's no external power supply during programing via USB port, you need to short the VUSB by jumper cap so as to supply the module with working voltage.
5. The load current of the heater cartridge and the fan interfaces shall not exceed the maximum withstand current to prevent the MOS tube from being burned out.

## 6 FAQ

Q: What's the maximum current for the heater cartridge and fan interface?

A: The maximum output current of the heater cartridge interface: 5A.

The maximum output current of the fan interface: 1A.

The total current for the heater cartridge, driver and fan needs to be less than 6A.

## BIGTREETECH

21 / 21

Q: Cannot update firmware via USB port?
A: You need to make sure that the jump cap is plugged on VUSB, and the indicator light on the board is on.

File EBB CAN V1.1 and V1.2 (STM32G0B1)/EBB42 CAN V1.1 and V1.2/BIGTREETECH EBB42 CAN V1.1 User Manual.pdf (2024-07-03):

Shenzhen Big Tree Technology Co., Ltd.

## BIGTREETECH

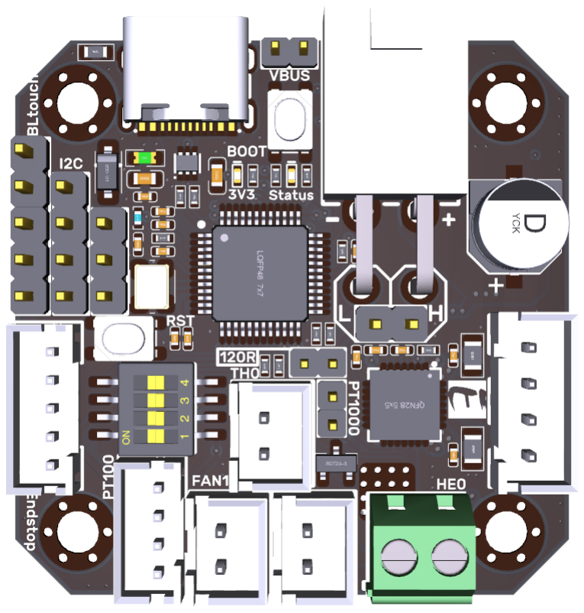
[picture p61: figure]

1 / 21

# BIGTREETECH

# EBB42 CAN V1.1 User Manual

## BIGTREETECH

2 / 21

## Contents

## BIGTREETECH

3 / 21

## Revision History

Revision | Description | Date
01.00 | First Draft | 2022/05/16
01.01 | CAN bus recommendation speed increased from 250K to 1M | 2024/07/02

## BIGTREETECH

4 / 21

## 1 Brief Introduction

BIGTREETECH EBB42 CAN V1.1 is a nozzle adapter board made by the 3D printing team of Shenzhen Big Tree Technology Co., Ltd. for a 42 stepper motor extruder. It can communicate via a USB or CAN, which greatly simplifies wiring.

### 1.1 Main Features

1. With a BOOT and RESET buttons reserved, users can update the firmware via DFU mode by USB.
2. Adding a protection circuit on the thermistor avoids burning the main control chip caused by the electric leakage of the heater cartridge.
3. The thermistor can select the pull-up resistor value via a jumper, in this way, it can support PT1000 (2.2K pull-up resistor), which is convenient for DIY.
4. The USB power is selected through a jumper cap, which effectively isolates the motherboard DC-DC and USB 5V.
5. Reserve the I2C interface, this interface can also be used for filament runout/blocking detection, or DIY for other functions.
6. A follow current diodes are added to the inductive load interface (fan) to ensure that when the fan MOS is turned off, the fan winding current has a follow current loop, which effectively prevents the high voltage generated by the winding drain at the MOS tube when it is turned off. Considering the size of the board and the switch characteristics of the extruder fan, a Schottky diode in a SOD-323 package is used.
7. The DCDC step-down circuit is reversely connected to a diode to prevent the subsequent circuit from being damaged due to the reverse connection of the power line.
8. Onboard MAX31865 (optional function, the version without 31865 does not have this function, but there are reserved pads), supports 2-wire/4-wire PT100/PT1000 selection.
9. Support communication via CAN or USB. The terminal resistor 120R of CAN can be selected through a jumper cap, and it reserves a CAN expansion interface.
10. Equipping the ESD protection chip on the USB port prevents the main control from being broken down by the static electricity of the USB port.
11. Limit switch hardware debouncing circuit.

## BIGTREETECH

5 / 21

12. The adaptor board is equipped with terminals, female reeds, double-way studs and screws, which are required for DIY, greatly meeting the DIY needs of customers.
13. Support CAN bus connection, which has long data transmission, strong anti-noise ability, strong real-time performance and high reliability.

### 1.2 Product Parameters

1. Product Size: 40mm x 40mm, for further details please read: BIGTREETECH EBB42 CAN V1.1-SIZE.pdf
2. Installation Dimensions: Hole Spacing 31mm x 31mm, M3 Screw Holes x 4
3. Microprocessor: ARM Cortex-M0+ STM32G0B1CBT6 64MHz
4. Input Voltage: DC12V-DC24V 9A
5. Logic Voltage: DC 3.3V
6. Heating Interface: Heater Cartridge (E0), maximum output current: 5A
7. Onboard Sensor: ADXL345
8. Fan Interfaces: Two CNC Fans (FAN0, FAN1)
9. Maximum Output Current of Fan Interface: 1A, Peak Value: 1.5A

10.Expansion Interfaces: EndStop, I2C, Probe, RGB, PT100/PT1000, USB Interface, CAN Interface

11.Motor Drive: Onboard TMC2209, Hardware Address: 00, Rsense: 0.11R

12. Driver Working Mode: UART

13.Stepper Motor Interface: E

14.Temperature Sensor Interface Optional: One for 100K NTC or PT1000(TH0), one for PT100/PT1000

15.USB Communication Interface: USB-Type-C

16.DC-DC 5V Maximum Output Current: 1.5A

### 1.3 Firmware Support

This product currently only supports Klipper.

## BIGTREETECH

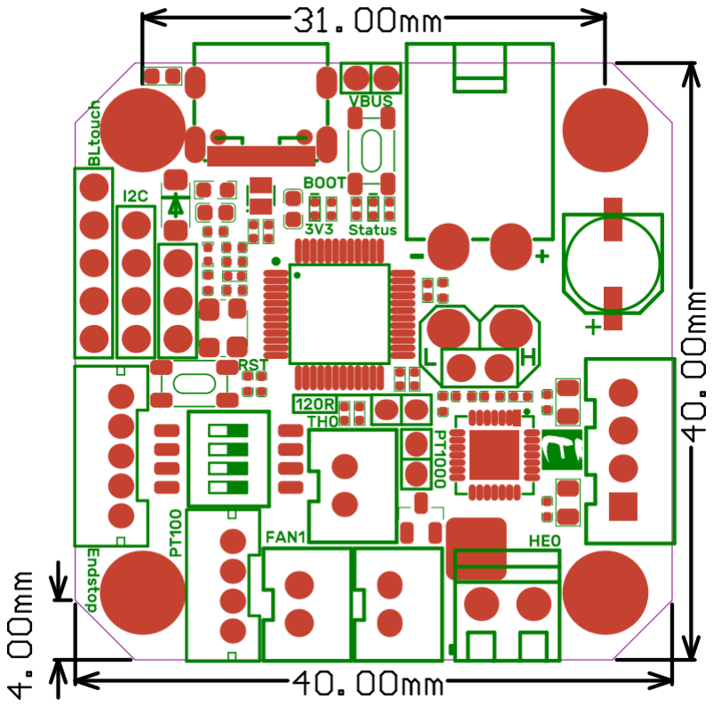
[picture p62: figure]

6 / 21

### 1.4 Product Size

## BIGTREETECH

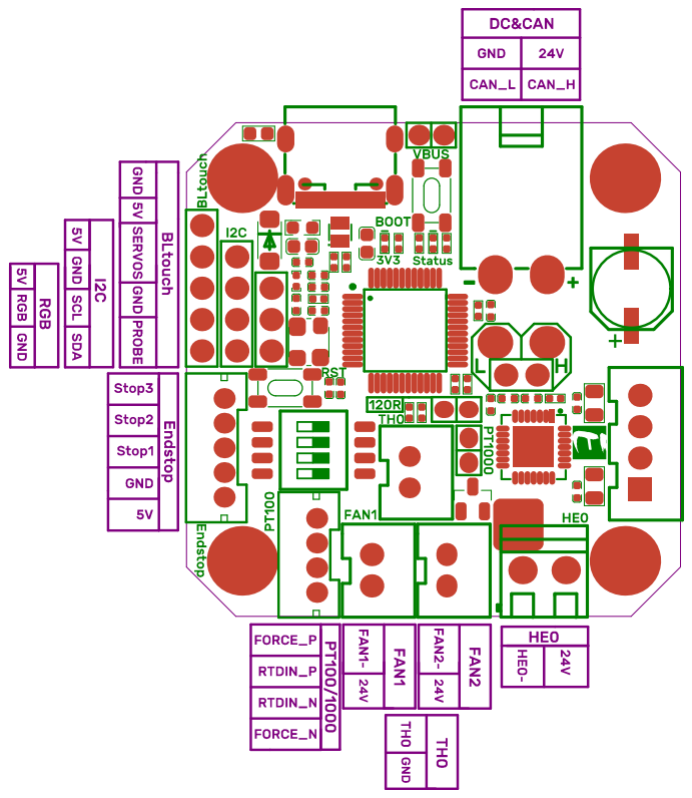
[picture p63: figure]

7 / 21

## 2 Peripheral Interface

### 2.1 Pin Instruction

## BIGTREETECH

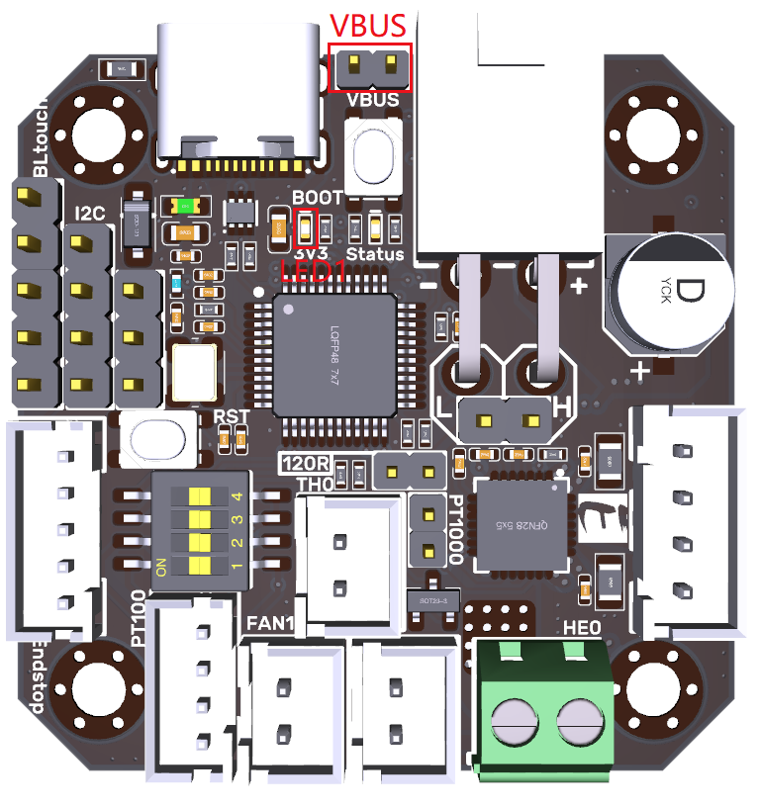
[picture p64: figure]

8 / 21

## 3 Introduction of Interface

### 3.1 Power up via USB

After the motherboard is powered on, the yellow-green LED1 lights will light up, indicating a normal power supply. The VUSB in the middle of the board is the power selection part. Only when using USB to supply power to the motherboard or need to supply power through USB, do you need to use the jumper cap to connect VUSB.

## BIGTREETECH

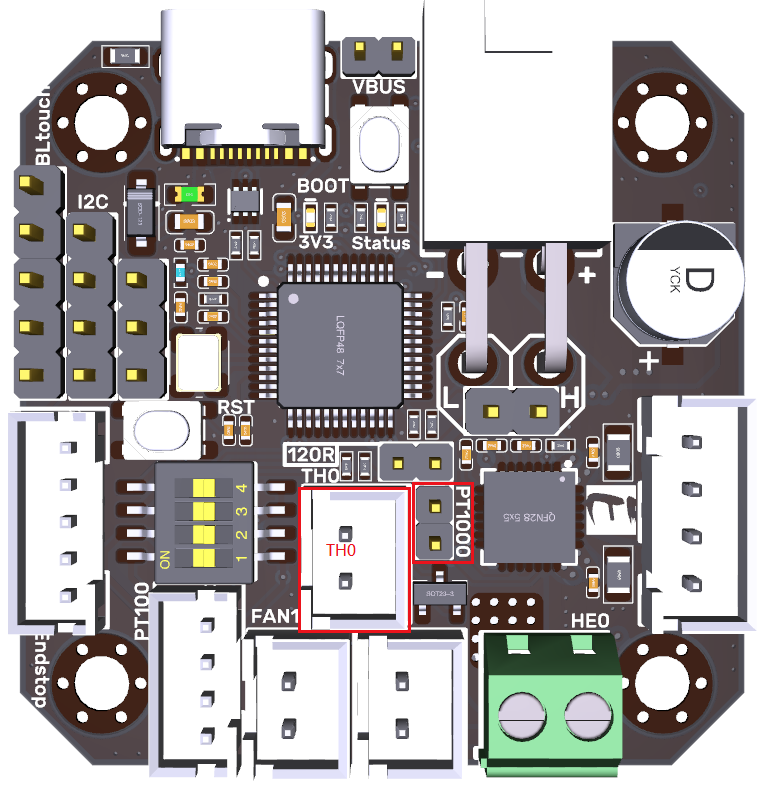
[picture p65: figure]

9 / 21

3.2 100K NTC or PT1000 Settings

1. Version without 31865: No need to plug a jumper cap when using a 100K NTC thermistor, and TH0's pull-up resistor value is 4.7K. When using PT1000, you need to use the jumper cap to short the two pins, as shown below picture. At this time, TH0's pull-up resistor value is 2.2K (Notice: the temperature accuracy that's read out this way will be less accurate than that of MAX31865).
2. Version with 31865: Select PT100/PT1000 by DIP switch, two-line or four-wire:
1 | 2 | 3 | 4 | Sensor Model
ON | ON | ON | OFF | Two lines PT100
ON | ON | OFF | ON | Two lines PT1000
OFF | OFF | ON | OFF | Four-wire PT100
OFF | OFF | OFF | ON | Four-wire PT1000

## BIGTREETECH

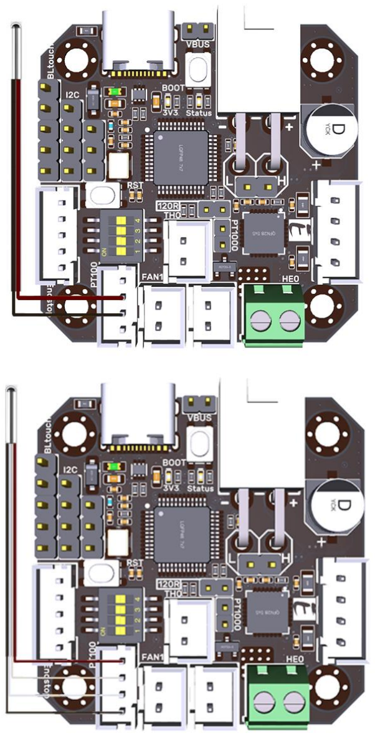
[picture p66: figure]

10 / 21

## BIGTREETECH

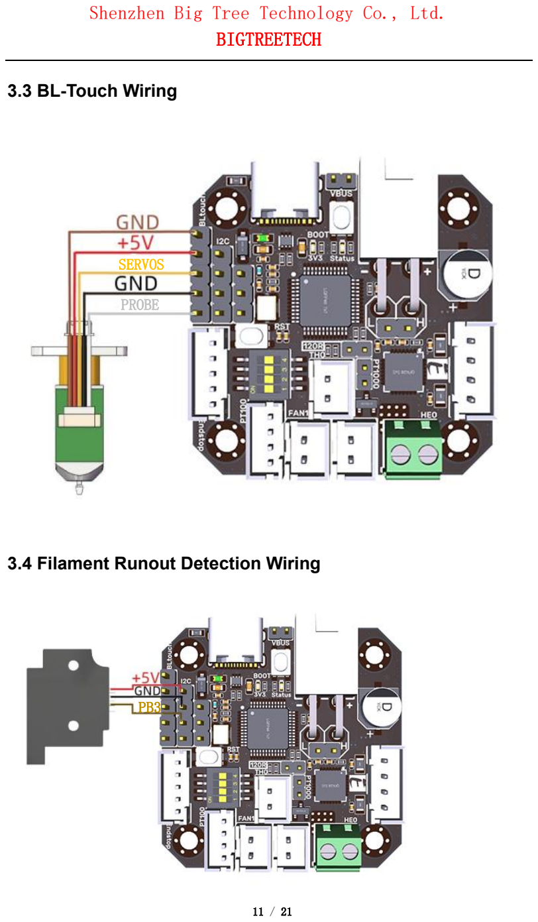
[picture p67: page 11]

11 / 21

### 3.3 BL-Touch Wiring

### 3.4 Filament Runout Detection Wiring

SERVOS

PROBE

PB3

## BIGTREETECH

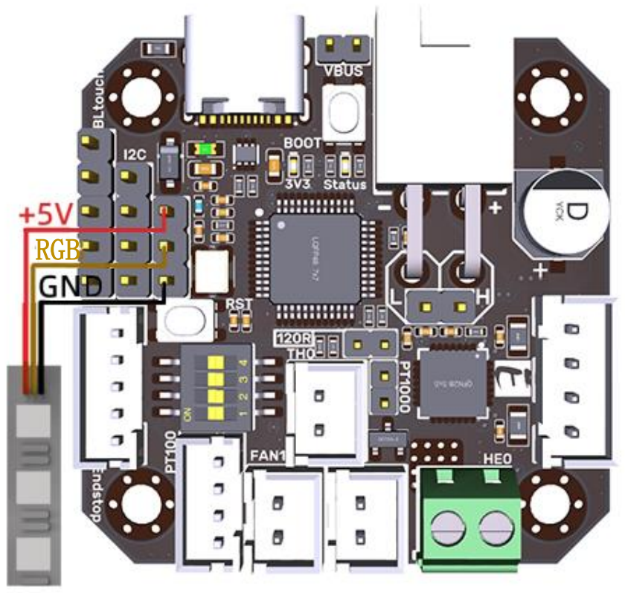
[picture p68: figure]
RGB

12 / 21

### 3.5 RGB Wiring

## BIGTREETECH

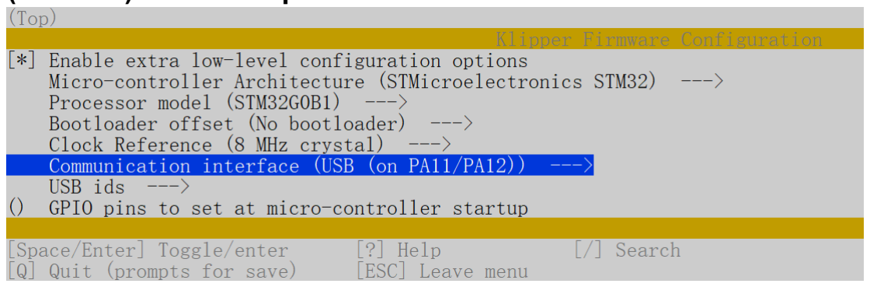
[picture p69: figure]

13 / 21

## 4 Klipper

### 4.1 Firmware Compilation

1. After connecting to the Raspberry Pi via SSH, type the below sentences at the command line:
cd ~/klipper/
make menuconfig
Compile the firmware with the following configuration (if the following options are not available, please update the Klipper source to the latest version). [*] Enable extra low-level configuration options
Micro-controller Architecture (STMicroelectronics STM32) ---> Processor model (STM32G0B1) --->
Bootloader offset (No bootloader) --->
Clock Reference (8 MHz crystal) --->
If using USB communication over Type-C Communication interface (USB (on PA11/PA12)) ---> If using CANBus communication
Communication interface (CAN bus (on PB0/PB1)) ---> (1000000) CAN bus speed
2. When the configuration is completed, type 'q' to exit the configuration interface. Select "Yes" when asked whether to save the configuration.
3. Enter make to compile the firmware. The 'klipper.bin' firmware that we need
will be generated on the | home/pi/klipper/out | folder of the Raspberry Pi when
completed. The firmware is on the left side of SSH software, users can download it directly to the computer.

## BIGTREETECH

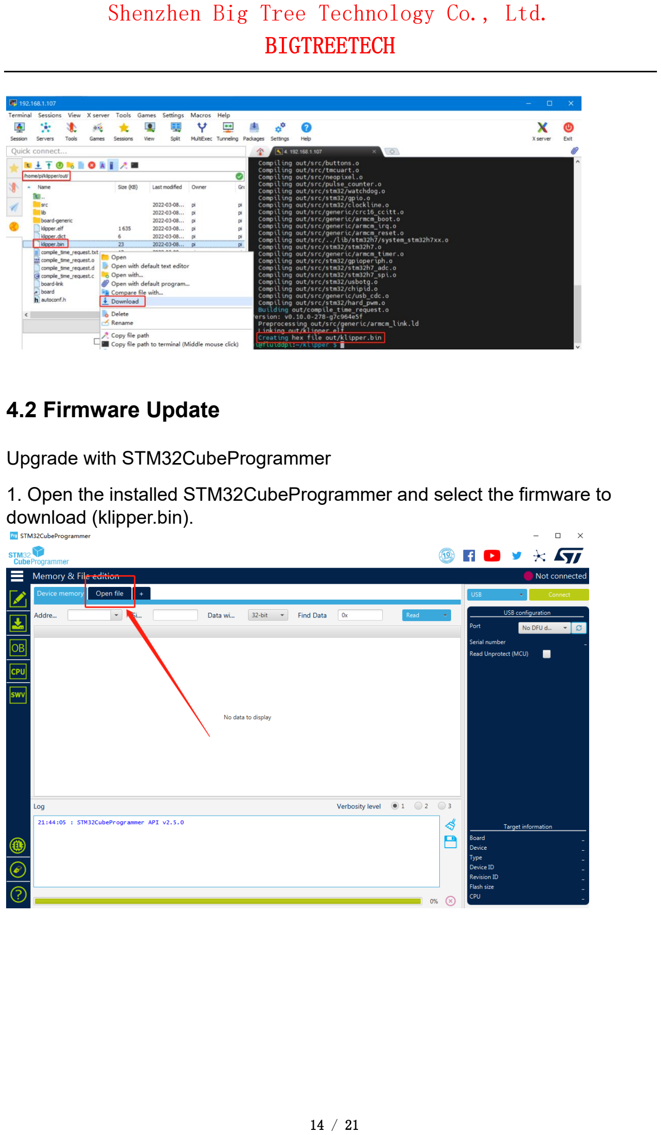
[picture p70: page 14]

14 / 21

### 4.2 Firmware Update

Upgrade with STM32CubeProgrammer

1. Open the installed STM32CubeProgrammer and select the firmware to download (klipper.bin).

## BIGTREETECH


15 / 21

2. Press and hold the Boot button, then click the RST button to enter DFU mode.
3. Click the "Refresh" button in the STM32CubeProgrammer until the Port changes from "No DFU d..." to "USB1", then click "Connect" to connect the chip.

## BIGTREETECH


16 / 21

4. After the connection is successful, "Connect" will change into "Disconnect", and then click "Download", after the download is completed, a pop-up window of "File download complete" will appear, indicating that the writing is successful.

### 4.3 CANBus Configuration

### 4.3.1 Work with BIGTREETECH U2C:

1. Type the following command | sudo nano /etc/network/interfaces.d/can0 | in the
SSH terminal and execute:

auto can0
iface can0 can static
bitrate 1000000
up ifconfig $IFACE txqueuelen 1024

## BIGTREETECH


17 / 21

Set the speed for CANBus at 1M(must be the same as the speed set in the
firmware | (1000000) CAN bus speed), Save(Ctrl + S)after modification and
exit(Ctrl + X), Type | | sudo rebootto to reboot Raspberry Pi.
2. Every device on CANBus will generate a canbus_uuid based on MCU's UID. If users want to find the ID for every microcontroller, please make sure the hardware is powered on and wired correctly, then run the following command: ~/klippy-env/bin/python ~/klipper/scripts/canbus_query.py can0
3. If detected an uninitialized CAN device, the above command will report the device's canbus_uuid:
Found canbus_uuid=0e0d81e4210c
4. If Klipper operates normally and is connected to the device, then it won’t report canbus_uuid, which is also normal.

### 4.3.2 Work with BIGTREETECH RPI-CAN HAT:

1. Type and run the following command sudo nano /boot/config.txt, and added below contents on file config.txt.
dtparam=spi=on
dtoverlay=mcp2515-
can0,oscillator=12000000,interrupt=25,spimaxfrequency=1000000
After modification, save(Ctrl + S)and exist(Ctrl + X), type | sudo reboot | to
reboot Raspberry Pi.
2. Type and run commands dmesg | grep -i '\(can\|spi\)' to test if RPI-CAN HAT
module is normally connected. The normal response should be as below:

[ 8.680446] CAN device driver interface
[ 8.697558] mcp251x spi0.0 can0: MCP2515 successfully initialized.

## BIGTREETECH


18 / 21

[ 9.482332] IPv6: ADDRCONF(NETDEV_CHANGE): can0: link becomes ready

3. Type | sudo nano /etc/network/interfaces.d/can0 | on the SSH terminal and run
the command.
auto can0
iface can0 can static
bitrate 1000000
up ifconfig $IFACE txqueuelen 1024
Set the speed for CANBus at 1M(must be the same as the speed set in the firmware (1000000) CAN bus speed). Save (Ctrl + S) after modification and
exit (Ctrl + X). Type command | sudo reboot | to reboot Raspberry Pi.
4. Every device on CANBus will generate a canbus_uuid base on MCU's UID. If users want to find the ID for every microcontroller, please make sure the hardware is powered on and wired correctly, then run the following command: ~/klippy-env/bin/python ~/klipper/scripts/canbus_query.py can0
5. If detected an uninitialized CAN device, the above command will report the device's canbus_uuid:
Found canbus_uuid=0e0d81e4210c
6. If Klipper operates well and is connected to the device, then it won't report the canbus_uuid, which is normal.

## BIGTREETECH


19 / 21

### 4.4 Klipper Configuration

1. Enter the IP access of Raspberry Pi in the browser of the computer, and download the reference configuration of the motherboard from the file path shown in the figure below. If you cannot find this file, please update the Klipper firmware source code to the latest version, or download it from GitHub: https://github.com/bigtreetech/EBB (https://github.com/bigtreetech/SKR-3)
2. Upload the motherboard's configuration files to the Configuration Files.
3. Add the motherboard's configuration to the file "printer.cfg". [include sample-bigtreetech-ebb-canbus-v1.1.cfg]

## BIGTREETECH

20 / 21

4. Revise the ID number of the configuration files as the actual ID of the motherboard (USB serial or CANBus).
5. Configure the specific functions of the module as instructed below:

https://www.klipper3d.org/Overview.html

## 5 Cautions

1. When the TH0 interface doesn't work with PT1000, you can't plug a jump cap on it, otherwise 100K NTC won't work.
2. When using CAN communication, you need to see whether it is used as a terminal. If it is, you must plug a jumper cap on the 120R position.
3. When DIY crimping, wire according to the silkscreen, and DIY according to the Pin and Schematic diagrams so as to avoid the power line from being reversely connected or connected to the CAN signal, which will get the module burned.
4. If there's no external power supply during programming via USB port, you need to short the VUSB by jumper cap so as to supply the module with working voltage.
5. The load current of the heater cartridge and the fan interfaces shall not exceed the maximum withstand current to prevent the MOS tube from being burned out.

## 6 FAQ

Q: What's the maximum current for the heater cartridge and fan interface?

A: The maximum output current of the heater cartridge interface: 5A.

The maximum output current of the fan interface: 1A.

The total current for the heater cartridge, driver and fan needs to be less than 9A.

## BIGTREETECH

21 / 21

Q: Cannot update firmware via USB port?
A: You need to make sure that the jump cap is plugged on VUSB, and the indicator light on the board is on.

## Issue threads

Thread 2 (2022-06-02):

Max31865 Overvoltage or undervoltage fault

710920772, 2022-06-02:
Max31865 Overvoltage or undervoltage fault
Once the underlying issue is corrected, use the
"FIRMWARE_RESTART" command to reset the firmware, reload the
config, and restart the host software.
Printer is shutdown

When i was printting,It suddenly appeared!!!!!
I don't konw why????????????
the wire connected solid! And no indication towards Leakage!It just suddenly happen!!!!!!!!

Voodoobrew101, 2022-10-09:
If you power by a smart usb charger, the power in usb c is not fixed. I don't know what controlls it. But I suspect the charger is doing an assessment to decide what power to provide. Also faulty peripherals can cause or possibly housing power brownouts caused by say...a refrigerator compressor kicking on.

Get a proper pi power supply and the problem should go away. If you really never want to see it also get a battery backup with power conditioner.

se508, 2023-02-22:
I had the same issue and solved it.
It was on a Voron with Octopus Pro board. On the Voron the hotend is not grounded, so the potential is floating. With a heater connected even a very small leak current may be problematic.
One solution is to ground the hotend to 0v rail.
Another is to ensure there is no leak current from the heater to the sensor (replacing the heater in my case).

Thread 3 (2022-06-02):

Communication timeout during homing probe

710920772, 2022-06-02:
Communication timeout during homing probe

McPrince96, 2022-06-14:
Did you find a solution in the meantime? I ran into ai similar timeout but with x homing.

Looking at when your issue was opened i don't believe BTT is very active here. *sigh*

murphytodd4, 2022-09-09:
I had the same issue and ended up increasing my CAN baud rate to 500000. I still have the error once in a while but it is far more stable. I was also not able to run an resonance test successfully before increasing the rate.

basha318i, 2022-09-17:
> I had the same issue and ended up increasing my CAN baud rate to 500000. I still have the error once in a while but it is far more stable. I was also not able to run an resonance test successfully before increasing the rate.

Hi, I have the same issue but it’s happening quite frequently! I’m at 500,000 baud right now & not able to complete a single z-tilt!
Which version do you have on the U2C? The one on BTT github?

murphytodd4, 2022-09-17:
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

I believe I said that wrong. I set it to 500000 in the device tree setup but then ran my boards at 250000. I reflashed my firmware today at 500000 and the issue came back.

I am also just running a generic CAN to SPI breakout board.

McPrince96, 2022-09-17:
I'm not really sure what the solution was for me but this is what i did:
- Complete fresh install
- Orange Pi 3 lts instead of rpi zero
- Other higher quality usb cables

Be sure to watch this [this video](https://youtu.be/_FELCN8CbWA) . The can software mentioned in the btt manual is crap and installation is a pain in the ass. The can software mentioned in the video didn't used to support the Gb0 chip but now it should support it.

Voodoobrew101, 2022-10-09:
I have this error when my bed is too out of level. Try doing a manual level first.

Also give the z min travel -5. Sorry don't have exact parameter name on phone.

murphytodd4, 2022-10-09:
I ended up following this reply [here](https://klipper.discourse.group/t/canbus-communication-timeout-while-homing-z/3741/3) and I have not had another timeout error while trying to home

TURNERO, 2022-11-13:
I got this and it got worse over time. I was tearing my hair out. I kept getting undervoltage errors on my PI which was causing it to throttle. I was using a tablet plugged into one of the USB ports on the PI as a screen. Unplugging that seems to have fixed it.

emersonsc, 2023-02-06:
> I ended up following this reply [here](https://klipper.discourse.group/t/canbus-communication-timeout-while-homing-z/3741/3) and I have not had another timeout error while trying to home.
>
> Basically changing TRSYNC_TIMEOUT value in “/home/pi/klipper/klippy/mcu.py” file from 0.025 to 0.050

Tried that, didnt help for me.

Voodoobrew101, 2023-02-07:
My problem was bad plug conection. If you wiggle it and the light goes
off...

On Mon, Feb 6, 2023, 3:43 PM Emerson Corder ***@***.***>
wrote:

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

LobodPl, 2023-03-25:
If you are using "dockable_probe.py" module. Take a look [here ](https://github.com/Klipper3d/klipper/pull/4328#issuecomment-1476612792).

Tom-T, 2023-04-15:
> I ended up following this reply [here](https://klipper.discourse.group/t/canbus-communication-timeout-while-homing-z/3741/3) and I have not had another timeout error while trying to home.
>
> Basically changing TRSYNC_TIMEOUT value in “/home/pi/klipper/klippy/mcu.py” file from 0.025 to 0.050

This seems to have resolved my issue. Thank you for posting about it. :)

florianmuetzel, 2023-05-06:
I had the same today. But I am not using can. I Am using just the usb connection.  My problem was also a bad connection! A little bit of hot glue on the dupont plug resolved the problem

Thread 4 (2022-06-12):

Pin names for v1.1

McPrince96, 2022-06-12:
I can't find the pin names (like PA1, PB1, etc) for version 1.1. Version 1.0 does have this file/picture.
For v1.1 I can only find a pin file with the names (litteral names like "fan" and "rgb" etc) for each port.

Is it possible to share this file/picture? I would like to add the x_endstop but it can't find the pin name and it's not in the sample cfg file neither.

McPrince96, 2022-06-14:
Solved! Found the solution in the schematic file. I used the pin next to ground which is PB6.

Ran into other issue with this though which causes me to use the mainboard (pico) x endstop port. See issue #5

Closed 2022-06-14.

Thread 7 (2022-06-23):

EBB42 V1.1 STM32G0B1: MCU 'EBBCan' shutdown: Timer too close

cristianku, 2022-06-23:
I am running a Voron 2.4 with Octopus Pro 1.0, BTT U2C 1.1 and EBB42 1.1 STM32G0B1

All are with the latest firmware.

I am running the EBB42 with 4 wires from the U2C, using can bus communication.

I am also running a can bus communication, using a usb cable, from U2C to Octopus pro 1.0

I have set the can bus everywhere to 250000.

The error is repeatable over and over again, and always at the same point of the print. It actually starts after printing few layers, if my print is only few layers height , it doesn't appear.

So its not an overload . the raspberry pi 4 2gb I am using has 30% used CPU and 12% memory load... its not here the problem I think.

Can it be something in EBB42 from BigTreetech ?

and now after printing fine for few minutes, I am getting this error :

16:45:19
MCU 'EBBCan' shutdown: Timer too close

16:45:19

MCU 'EBBCan' shutdown: Timer too close
This often indicates the host computer is overloaded. Check
for other processes consuming excessive CPU time, high swap
usage, disk errors, overheating, unstable voltage, or
similar system problems on the host computer.
Once the underlying issue is corrected, use the
"FIRMWARE_RESTART" command to reset the firmware, reload the
config, and restart the host software.
Printer is shutdown

[https://github.com/Klipper3d/klipper/issues/5595](url)

cristianku, 2022-06-23:
Solution ! the can communication between Bigtreetech U2C and OCTOPUS pro 1.0 STM32F4  is not working !!!!
I switched back to serial and everything is working fine ! . I will try with the can communication using the branch https://github.com/KevinOConnor/klipper-dev/tree/work-usbcan-20220608 , so directly connecting via usb cable from raspberry and Octopus instead of using the U2C.

BUT ! the EBB42 still connected through U2C is working fine !.

I will try also for EBB42 using the branch above to connect directly from RJ11 on the Octopus Board instead  of going through U2C

Closed 2022-06-23.

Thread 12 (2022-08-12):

I2C timeout error

DrumClock, 2022-08-12:
I connected an OLED display to the I2C connector (which works with the I2C printer motherboard)

klipper configuration:

```
[display oled_1]
display_group: _toolhead_0
lcd_type: ssd1306
i2c_mcu: EBBCan_0   # mcu EBBCan_0
i2c_bus: i2c1             # u'BUS_PINS_i2c1': u'PB6,PB7'
i2c_address: 60         # 0x3C
contrast: 230            # range from 0 to 256
```

Unfortunately, I still get a timeout error on the i2C.
I tried SDA/SCL both PB3,PB4 and PB6,PB7.

![ebb](https://u
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
ser-images.githubusercontent.com/64655979/184295294-7fe01e2e-0372-4e18-9494-0a29e100f540.PNG)
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

DrumClock, 2022-08-25:
pull up resistors are not connected to the i2C bus!
Even if I add them, there is still no communication between Kipper and EBB

**MCU 'EBBCan0' shutdown: i2c timeout**

[klippy (10).log](https://github.com/bigtreetech/EBB/files/9422083/klippy.10.log)

ldr, 2023-02-15:
hi, did you get this to work ? i am unable to use pb3/pb4 pins either on ebb42 board

DrumClock, 2023-02-17:
Hi @ldr
it works fine for me on two EBB42 boards.
Do you have the current version of FW Klipper?

floodo1, 2023-06-19:
Also works fine for me (with recent firmware) when I specify the i2c pins:

```
[display ebb1106]
lcd_type: sh1106
i2c_mcu: EBBCan # The name of the micro-controller that the chip is connected to.
i2c_address: 60 # 0x3C
i2c_software_scl_pin: PB3
i2c_software_sda_pin: PB4
```

I believe `i2c_bus` cannot be used because pins PB3 and PB4 are defaulted to the SPI bus. Visible in the constants screenshot (under "BUS_PINS_spi3") and in Klipper source [I2C](https://github.com/Klipper3d/klipper/blob/master/src/stm32/i2c.c) and [SPI](https://github.com/Klipper3d/klipper/blob/master/src/stm32/spi.c)

Note: I ran into errors until I realized the i2c address on the silkscreen of my OLED screen was wrong!

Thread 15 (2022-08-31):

What is the pitch of the Pin Header Jumper Cap, so I can order a replacement jumper cap

GadgetAngel, 2022-08-31:
What is the pitch of the Pin Header Jumper Cap for the EBB36 and EBB42 boards?
My box spilled and I lost all the jumper caps. I need to order a replacement jumper caps but the jumper caps for the EBB36 are not 2.54mm pitch.  What is the pitch for these jumper caps?

gielbloks, 2022-09-01:
measure with a caliper / google pcb jumper spacings or something should be easy to find..

if you're in a rush.. carefully bridge them with a small drop of solder (one way action in most cases as it can be hard to remove an don't melt the plastic)

GadgetAngel, 2022-09-02:
> measure with a caliper / google pcb jumper spacings or something should be easy to find..
>
> if you're in a rush.. carefully bridge them with a small drop of solder (one way action in most cases as it can be hard to remove an don't melt the plastic)

I tried the jumper cap with pitch 1.27mm but those are way too small.  I just order some with a pitch of 2mm and I will post if those worked when they arrive

gielbloks, 2022-09-02:
or just bridge it with a drop of solder..

ey wait . there are enough crimp contacts in the set.. crimp 2 together and use it as a bridge.. surely for the time being/solder the 2 crimp connectors together and you will have a jumper..

groeten/regards

Giel Bloks

Vergert 81
6662DX ELST
________________________________
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

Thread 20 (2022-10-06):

Connecting to BTT Hermitcrab CAN-Distribution Board via USB-C Destroys EBB42 v1.2 board

Voodoobrew101, 2022-10-06:
This happened to me 2/2 times.

First attempt. I flashed CanBus Bootloader as with Communication interface (CAN bus (on PB0/PB1)) not paying attention thinking it was can-USB. Plugged in EBB42 to BTT Hermit Crab CAN-Distribution Board with USB-C cable and no jumper on VBUS, no other cables connected. Turned on printer and could not find EBB42 with "python3 flash_can.py -q" in putty.  From this point on Board lights up but will not enter DFU and connect to STM32CubeProgremmer. Multiple attempts to connect with canbus have also failed.

Second attempt. I immediately connected new EBB42 to BTT Hermit Crab CAN-Distribution Board with USB-C cable and no jumper on VBUS, no other cables connected. I did not flash board with any firmware. Turned on printer and heard a tiny pop before BL-touch from Hermit Crab extruder began to cycle. Two USB boards connected to outputs on BTT Hermit Crab CAN-Distribution Board. Port 1 had complete working BTT Hermit Crab extruder/hotend/bltouch/fans, Port 2 had EBB42 v1.2 board with no jumpers. After pop it appears that Component D6 is burned as well as some traces that connect to C31 look wet (probably heat damage?).

I understand that the setup directions have not been followed but why did this happen? It should not be so easy to destroy these boards.

Is this because the wrong firmware is installed?
Is this because I did not connect VBUS jumper?
Is this because of the hardware from Hermit Crab is incompatible?

My Setup.
Klipper on Raspberry Pi connected to and powered by J26 on BTT Octopus 1.1
BTT Octopus 1.1 runs X,Y,Z0,Z1 and bed heater
Raspberry Pi has BTT RPT-CAN HAT from Hermit Crab CAN
Hermit Crab BTT RPT-CAN HAT connects to Hermit Crab CAN-Distribution Board
Hermit Crab CAN-Distribution Board connects to power supply and Hermit Crab CAN-extruder with extruder/hotend/bltouch/fans connected

Voodoobrew101, 2022-10-09:
Ok, so you can't run 24v can to the usb-c. It will totally burn up the EBB.

I cut a 4 wire usb cable and wired it to the included can conector to make an adapter, it works great. Try to find a fat one with thicker wires.

I used a ohm meter to find which usb wire was which while probing the splitter board and referring to the 3d pdf schematic with traces.

Voodoobrew101, 2022-10-09:
The fact that you can't cross these usb-c cables from one of your devices to another should be in the manual with big red letters!

Benkult, 2023-03-24:
What's written on every hardware manual, is pinout.

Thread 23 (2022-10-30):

MCU 'EBBCan' shutdown: Missed scheduling of next digital out event

AlvinF01, 2022-10-30:
Randomly shutdown with message:
MCU 'EBBCan' shutdown: Missed scheduling of next digital out event

Canbus:
EBB36 CAN V1.2

U2C:
U2C 2.1

Klipper Version:
v0.10.0-613-gebc3b0de

Both Canbus and u2c is the latest one with STM32G0B1 chipset
Canbus firmware based on manual config using 250k bitrate
U2C firmware using the V2 firmware from github
https://github.com/bigtreetech/U2C/blob/master/firmware/U2C_V2_STM32G0B1.bin

/etc/network/interfaces.d/can0
```
allow-hotplug can0
iface can0 can static
 bitrate 250000
 up ifconfig $IFACE txqueuelen 1024
```

Klipper.log
```
Stats 2394.8: gcodein=0  mcu: mcu_awake=0.007 mcu_task_avg=0.000010 mcu_task_stddev=0.000009 bytes_write=1688503 bytes_read=1079206 bytes_retransmit=9 bytes_invalid=0 send_seq=54108 receive_seq=54108 retransmit_seq=2 srtt=0.001 rttvar=0.000 rto=0.025 ready_bytes=51 stalled_bytes=0 freq=180001025 EBBCan: mcu_awake=0.015 mcu_task_avg=0.000018 mcu_task_stddev=0.000028 bytes_write=500821 bytes_read=285546 bytes_retransmit=782 bytes_invalid=0 send_seq=13336 receive_seq=13336 retransmit_seq=13310 srtt=0.005 rttvar=0.003 rto=0.025 ready_bytes=45 stalled_bytes=0 freq=63999174 adj=63998877 rpi: mcu_awake=0.000 mcu_task_avg=0.000008 mcu_task_stddev=0.000012 bytes_write=15258 bytes_read=48941 bytes_retransmit=0 bytes_invalid=0 send_seq=2519 receive_seq=2519 retransmit_seq=0 srtt=0.000 rttvar=0.000 rto=0.025 ready_bytes=0 stalled_bytes=0 freq=50000064 adj=49999756 sd_pos=584197 heater_bed: target=100 temp=99.7 pwm=0.305 raspberry_pi: temp=45.1 mcu_temp: temp=40.8 sysload=0.24 cputime=197.063 memavail=669104 print_time=2399.725 buffer_time=2.124 print_stall=0 extruder: target=245 temp=245.0 pwm=0.735
Stats 2395.8: gcodein=0  mcu: mcu_awake=0.010 mcu_task_avg=0.000011 mcu_task_stddev=0.000009 bytes_write=1690654 bytes_read=1079756 bytes_retransmit=9 bytes_invalid=0 send_seq=54152 receive_seq=54152 retransmit_seq=2 srtt=0.001 rttvar=0.000 rto=0.025 ready_bytes=0 stalled_bytes=0 freq=180001017 EBBCan: mcu_awake=0.015 mcu_task_avg=0.000018 mcu_task_stddev=0.000028 bytes_write=502130 bytes_read=285756 bytes_retransmit=782 bytes_invalid=0 send_seq=13359 receive_seq=13359 retransmit_seq=13310 srtt=0.006 rttvar=0.003 rto=0.025 ready_bytes=0 stalled_bytes=0 freq=63999167 adj=63998927 rpi: mcu_awake=0.000 mcu_task_avg=0.000008 mcu_task_stddev=0.000012 bytes_write=15264 bytes_read=48957 bytes_retransmit=0 bytes_invalid=0 send_seq=2520 receive_seq=2520 retransmit_seq=0 srtt=0.000 rttvar=0.000 rto=0.025 ready_bytes=0 stalled_bytes=0 freq=50000063 adj=49999770 sd_pos=584804 heater_bed: target=100 temp=99.7 pwm=0.305 raspberry_pi: temp=44.0 mcu_temp: temp=40.8 sysload=0.22 cputime=197.161 memavail=669224 print_time=2400.726 buffer_time=2.125 print_stall=0 extruder: target=245 temp=245.1 pwm=0.735
Stats 2396.8: gcodein=0  mcu: mcu_awake=0.010 mcu_task_avg=0.000011 mcu_task_stddev=0.000009 bytes_write=1694367 bytes_read=1080435 bytes_retransmit=9 bytes_invalid=0 send_seq=54222 receive_seq=54222 retransmit_seq=2 srtt=0.001 rttvar=0.000 rto=0.025 ready_bytes=39 stalled_bytes=0 freq=180001010 EBBCan: mcu_awake=0.015 mcu_task_avg=0.000018 mcu_task_stddev=0.000028 bytes_write=504023 bytes_read=286017 bytes_retransmit=1313 bytes_invalid=0 send_seq=13392 receive_seq=13389 retransmit_seq=13392 srtt=0.007 rttvar=0.003 rto=0.200 ready_bytes=244 stalled_bytes=11 freq=63999159 adj=63998858 rpi: mcu_awake=0.000 mcu_task_avg=0.000008 mcu_task_stddev=0.000012 bytes_write=15270 bytes_read=48973 bytes_retransmit=0 bytes_invalid=0 send_seq=2521 receive_seq=2521 retransmit_seq=0 srtt=0.000 rttvar=0.000 rto=0.025 ready_bytes=0 stalled_bytes=0 freq=50000063 adj=49999792 sd_pos=586083 heater_bed: target=100 temp=99.7 pwm=0.305 raspberry_pi: temp=44.0 mcu_temp: temp=40.8 sysload=0.22 cputime=197.286 memavail=669000 print_time=2401.909 buffer_time=2.306 print_stall=0 extruder: target=245 temp=245.2 pwm=0.682
toolhead: max_velocity: 300.000000
max_accel: 3000.000000
max_accel_to_decel: 1500.000000
square_corner_velocity: 5.000000
toolhead: max_velocity: 300.000000
max_accel: 1000.000000
max_accel_to_decel: 500.000000
square_corner_velocity: 5.000000
Stats 2397.8: gcodein=0  mcu: mcu_awake=0.010 mcu_task_avg=0.000011 mcu_task_stddev=0.000009 bytes_write=1697281 bytes_read=1081048 bytes_retransmit=9 bytes_invalid=0 send_seq=54279 receive_seq=54279 retransmit_seq=2 srtt=0.001 rttvar=0.000 rto=0.025 ready_bytes=28 stalled_bytes=0 freq=180001004 EBBCan: mcu_awake=0.015 mcu_task_avg=0.000018 mcu_task_stddev=0.000028 bytes_write=504023 bytes_read=286065 bytes_retransmit=1667 bytes_invalid=0 send_seq=13392 receive_seq=13389 retransmit_seq=13392 srtt=0.007 rttvar=0.003 rto=0.800 ready_bytes=244 stalled_bytes=810 freq=63999159 adj=63998777 rpi: mcu_awake=0.000 mcu_task_avg=0.000008 mcu_task_stddev=0.000012 bytes_write=15276 bytes_read=48989 bytes_retransmit=0 bytes_invalid=0 send_seq=2522 receive_seq=2522 retransmit_seq=0 srtt=0.000 rttvar=0.000 rto=0.025 ready_bytes=0 stalled_bytes=0 freq=50000063 adj=49999801 sd_pos=586791 heater_bed: target=100 temp=99.8 pwm=0.245 raspberry_pi: temp=44.5 mcu_temp: temp=40.7 sysload=0.22 cputime=197.369 memavail=670132 print_time=2402.613 buffer_time=2.009 print_stall=0 extruder: target=245 temp=245.2 pwm=0.682
MCU 'EBBCan' shutdown: Missed scheduling of next digital out event
```
```
Receive: 93 2396.416949 2396.393688 16: seq: 11, thermocouple_result oid=7 next_clock=3275030975 value=29314 fault=0
Receive: 94 2396.716818 0.000000 16: seq: 1d, thermocouple_result oid=7 next_clock=3294230975 value=29316 fault=0
Receive: 95 2397.017185 0.000000 16: seq: 1d, thermocouple_result oid=7 next_clock=3313430975 value=29318 fault=0
Receive: 96 2397.317321 0.000000 16: seq: 1d, thermocouple_result oid=7 next_clock=3332630975 value=29318 fault=0
Receive: 97 2397.617566 0.000000 16: seq: 1d, thermocouple_result oid=7 next_clock=3351830975 value=29318 fault=0
Receive: 98 2397.916577 0.000000 16: seq: 1d, thermocouple_result oid=7 next_clock=3371030975 value=29318 fault=0
Receive: 99 2398.116943 0.000000 12: seq: 1d, shutdown clock=3364630800 static_string_id=Missed scheduling of next digital out event
Transition to shutdown state: MCU 'EBBCan' shutdown: Missed scheduling of next digital out event
This is generally indicative of an intermittent
communication failure between micro-controller and host.
```

It seems shutdown during thermocouple

AlvinF01, 2022-10-31:
I only get 2 shutdown in first 2 day
Now it is stable for more than 10+ hours
I think maybe just my connection not stable enough

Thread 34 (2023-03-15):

Manta E3EZ+CB1+EBB36 v1.2

alexandrugai, 2023-03-15:
hi there...i need some help. yesterday arrived the ebb36 v1.2 and i'm trying to connect it to manta e3ez over can. manta flashed with klipper and selected "usb to can bus bridge (usb on PA11/PA12 and canbus on PB8/PB9)" and here begins the problem... when flashed this way, CB1 doesn't recognize manta anymore over "usb serial" connection. can0 network appears, but just the manta, not the ebb36. to mention that when i try to flash the ebb36 with stmcube i get an error "download failed" like in issue #32  or something like this but when i flash it with canboot, flashes ok (at least no error on download). in the manta manual i didn't found nothing about can bus. after first attempt to flash the ebb, it remains with one led full lit and the other one barely visible.

FlorinAnghel, 2023-03-16:
do this tutorial... it works without failure
https://maz0r.github.io/klipper_canbus/toolhead/ebb36-42_v1.1.html

alexandrugai, 2023-03-17:
yes...it works now. i was flashing the manta with wrong can pins under canbus comms. thank you

nicolas-lang, 2023-07-15:
Would you mind sharing your final cfg?
I have a similiar issue and cant find the ebb.
- Which pins did you select for Canbus in the Manta E3EZ-klipper-menuconfig
- Which physical connector did you use on the Manta E3EZ? The left one, labeled tx pb13/rx pb12 or the right one labeled canH/canL
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

maxcalavera81, 2025-03-22:
Good.  I also have this doubt.  Which connector on the blanket did you connect the ebb36 to?  Thank you very much in advance.

Closed 2023-03-17.

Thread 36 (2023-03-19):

Unable to read tmc uart 'extruder' register IFCNT

dogtrpp, 2023-03-19:
Replaced an EBB36 with the SB2209 and getting this error when I try to extrude.

"Unable to read tmc uart 'extruder' register IFCNT"

Extruder config (I changed the MCU name from EBBCan to can0)

## EXTRUDER
[extruder]
step_pin: can0: PD0
dir_pin: !can0: PD1
enable_pin: !can0: PD2
##  Update value below when you perform extruder calibration
##  If you ask for 100mm of filament, but in reality it is 98mm:
##  rotation_distance = <previous_rotation_distance> * <actual_extrude_distance> / 100
##  22.6789511 is a good starting point
rotation_distance: 22.68486
gear_ratio: 50:10 #for CW2
microsteps: 16
full_steps_per_rotation: 200 #1.8deg Motor
max_extrude_only_distance: 200.0
max_extrude_cross_section: 50.0
max_extrude_only_velocity: 75.0
max_extrude_only_accel: 1500
nozzle_diameter: 0.400
filament_diameter: 1.750
heater_pin: can0:PB13
sensor_pin: can0:PA3
sensor_type: ATC Semitec 104NT-4-R025H42G
#pullup_resistor: 2200             # this is the default for the Revo heater
#control: pid
#pid_Kp: 22.2
#pid_Ki: 1.08
#pid_Kd: 114
min_temp: 0
max_temp: 327
min_extrude_temp: 170
pressure_advance: .035

## EXTRUDER MOTOR
[tmc2209 extruder]
uart_pin: can0: PA15
stealthchop_threshold: 999999
run_current: 0.650

travisdieckmann, 2023-10-24:
I'm experiencing the same error and I see you closed the issue... What was the fix?

dogtrpp, 2023-10-24:
> I'm experiencing the same error and I see you closed the issue... What was the fix?

It's pretty silly. I thought I bought the version with the 2209 driver, but turns out it was the 2240. Changed the configuration in Klipper and it worked fine.

travisdieckmann, 2023-10-24:
🤦 I did THE SAME EXACT THING! 🤦

PkBrasil17, 2024-08-18:
and i did ... the exact same thing!!!!

Closed 2023-03-20.

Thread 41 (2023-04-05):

SB2209 Electrical Burning Smell

sergelhr, 2023-04-05:
After moving from tap mechanical switch to Voron OptoTap PCB v2.4.1 5-24V, an electrical burning smell was evident.
opto tap indication red/blue was ok. i didn't select 5 or 24v pad at the back of the pcb !
After returning to  mechanical switch no more smell (already burnt!), no evidence of heat damage onto opto tap or EBB, the only symptom rgb leds remains off! nil time so far to carry out a trouble shoot, might be front face was not in line with the connector ?

sergelhr, 2023-04-21:
after replacing the SB2209 pcb only, fault still present, leds remains off, after using a new EBB SB0000 CAN, and the new SB2209, LED working again.
Probably one chip linked to rgb port on SB0000 ,has burnt out. fixable ?

MyStoopidStuff, 2023-04-22:
I'm waiting on my EBB SB2209 to arrive, and also will be using the Optotap 2.4.1 board, so I am curious on how you set yours up.  It sounds like you are using the Optotap 2.4.1 using VCC (24v) and not 5v, since you mentioned you did not short the jumpers on the OptoTap, is that correct?  Were you connecting the OptoTap 2.4.1 to the proximity input on the SB2209 (and if that is the case, how was your proximity voltage jumper and npn/pnp jumpers set)?  Thanks!

sergelhr, 2023-04-22:
#MyStoopidStuff
voron tap wiring refer to
https://github.com/bigtreetech/EBB/blob/master/EBB%20SB2240_2209%20CAN/Build%20Guide/EBB%20SB2240%202209%20CAN%20v1.0%20Build%20Guide.pdf
page 17 (21 of 45)
And yes regarding optotap 2.4.1,for peace of mind, i cut the trace (24v) and make a bridge to 5v see info below
https://lab4450.com/product/voron-tap-probe/

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

sergelhr, 2023-04-22:
Just another issue with my new sb2209 and firmware klipper v0.11.0-180-g011b4e39 no more extrusion !
klippy log-> TMC extruder failed to init: Unable to read tmc uart 'extruder' register IFCNT
I've reverted to my previous sb2209 with firmware klipper Version: v0.11.0-148-g52f4e20c , no issue with extruder and led ok, so for sure the EBB SB0000 CAN was my issue.

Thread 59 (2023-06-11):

EBB SB2209 Heater not working?

Arkadije, 2023-06-11:
I managed to configure everything using the C2U adapter.
Everything works except the heater.
It does not give any signs of life. I have two different hotels with different heaters, so I can for sure say that it is not the faulty heater.
I just replaced the port in my config for all other sensors, so I did the same thing for the heater.
As I said, all other sensors, extruders, and end-stops are working only it does not want to start heating.

```
[extruder]
step_pin: EBBCan: PD0 #PB3
dir_pin: EBBCan: PD1 #PB4
enable_pin: !EBBCan: PD2 #!PD2
rotation_distance: 22.811396174424
gear_ratio: 50:10
microsteps: 16
full_steps_per_rotation: 200
nozzle_diameter: 0.400
filament_diameter: 1.75
heater_pin: EBBCan: PB13 #PC8
sensor_type: Generic 3950
sensor_pin: EBBCan: PA3 #PA0
min_temp: 10
max_temp: 280
max_power: 1.0
min_extrude_temp: 10
pressure_advance: 0.051835
max_extrude_only_distance: 400.0
```

italiann, 2023-09-30:
It is not working on my device as well

Arkadije, 2024-04-01:
Sadly now I haven't. While trying to figure out what the issue was, I let the magic smoke out, so I got a new one which was fine.

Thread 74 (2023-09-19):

SB2209 / SB2240 Won't go into DFU Mode

alexrizk1117, 2023-09-19:
I'm trying to install an sb2209 board using U2C wired into a pi. I'm trying to get the board into DFU mode but haven't had any success. All I see when running "lsusb" on my pi is:

- OpenMoko, Inc. stm32f445xx

- OpenMoko, Inc. Geschwister Schneider CAN adapter

Also, I'm trying to use the Boot + Reset method, but that doesn't seem to work. Is the SB2209 supposed to have a solid green and red light?

Also, when having the U2C board hooked up, should it be running power through the 24V PS, or should that only be powered through the pi in usb C?

Nooni99, 2023-10-18:
Have you found a solution @alexrizk1117 ? I am having the same issue except I see " Raspberry Pi RP2 Boot" when I try to go to DFU mode. Despite this, I am unable to enter dfu mode.

ga73, 2023-10-28:
@Nooni99 i'm having the same issue...have you worked this out ?

Nooni99, 2023-10-28:
@ga73 I have not found the exact solution and I just gave up on it because I wanted to get my printer working and just wired everything directly to my motherboard without canboot. However, I will do some experimenting once I have time. The next thing I am going to try which might work is using stm32 cube programmer to rewrite the sb2209. That might work and I suggest you try it. Let me know the results.

ga73, 2023-11-03:
Okay I got everything working last night and now up and running... I connected both the utc and rp2209 to 24v and ground instead of 5v usb power... The only other thing I did different was to get into dfu on the rp2209 I held down the boot button and then pressed the reset for maybe 3 second.. Let go of reset and then boot button... My can wires went to the screw terminals on the utc... Green was can low and yellow can high... I hope this helps someone

ga73, 2023-11-03:
Also make sure you remove the usb 5v jumper BEFORE connecting to 24v and that you have the 120r jumpers on both the utc and rp2209 board otherwise they won't communicate with each other

ga73, 2023-11-03:
Also this link was much better than just using the BTT guide alone...

https://github.com/Esoterical/voron_canbus

ga73, 2023-11-03:
Your welcome, I hope it helps, I'm not expert but feel free to leave another message here if you get stuck and I'll see what I did differently.. Good luck

ParabolicTech, 2024-02-09:
I am having the same issue. I hold the boot button and press the reset and it doesnt go into DFU mode. The device ID shows up with no description. This happens weather or not I try to enable DFU. I can plug it into my windows machine and it WILL bring up the bootloader folder if I do the button sequence. But for some odd reason connected to my Raspberry PI it doesnt function into DFU mode. Anyone else with this issue? Is there a way I can flash it in Windows?

Nooni99, 2024-02-09:
@ParabolicTech have you tried the solutions from above?

ParabolicTech, 2024-02-09:
> @ParabolicTech have you tried the solutions from above?

Yes, Thats why I posted. Ive been at this for hours in multiple places and cant figure out why I cant enable DFU. Diffrent known working cables - different (5v) power supplies, in fact I have my raspPI disconnected from my octopus board JUST to eliminate some of the other addresses showing up.

Nooni99, 2024-02-09:
@ParabolicTech hmmm. That's interesting. I'm not sure what's wrong. Those boards are quite difficult to get running anyways and I hope bigtreetech does another version that's easier to get working. In the mean time, I hope someone posts a solution that works for you. Best of luck!

ga73, 2024-02-09:
You mention you connected to 5v..have you tried connecting to 24v? This seemed to make a difference for me, also make sure your usb cable is a data and not just a usb power cable and finally do you have the r120 jumpers on both your canbus board AND your UTC (assuming this is what your using)?

I connected mine up fully and then flashed it, saying that if you just can't get it working try stm32cube software on windows as a last resort

xPakrikx, 2024-02-10:
same problem ... nothing helps. i see only Raspberry Pi RP2 Boot under lsusb.

LeighT616, 2024-02-17:
Hi i've just hit this issue... the board will not go into DFU mode.  I've tried various USB C cables and zero dice!

is there any resolution on this, i'm looking into the stm32cub software via windows but surely there has to be a better solution

ParabolicTech, 2024-02-17:
So after a lot of trials and tribulations I found out it DOES go into DFU mode by holding the reset button and clicking the boot button once. HOWEVER, the feedback that's listed online isn't correct. The board im using has the RP2040 chip on it so it wont list the description when it goes into DFU mode as listed on various instructions. The description is just blank. I was able to continue with the process and flashed the board, got the green light and the flashing red light and the rest of the listed setup worked fine.

rafal-molotkiewicz, 2024-03-28:
I have the same issue. My board only shows in two modes:

`Bus 001 Device 058: ID 1d50:614e OpenMoko, Inc. rp2040`
or
`Bus 001 Device 057: ID 2e8a:0003 Raspberry Pi RP2 Boot`

Neither one shows when I try `sudo dfu-util -l`

I tried holding boot and short pressing reset, long pressing reset, double and triple click reset.
I tried above swapping buttons.

I tried all this with 5V power, 24V power, and 24V power with connected CAN data lines.

Nothing made any difference. How can I proceed from here?

Nooni99, 2024-03-31:
Yeah, I'm still having the same issue with getting it in DFU mode. I have tried everything.

wes4560, 2024-04-30:
I have my sb2209 rb2040 hooked directly to the octopus using the rj connection I have unplugged everything used the 5v jumper and also tried the 24 v supply and I can't get it to go in DFU mode the light just stays green and I can't get it to show up at all in the ssh with the pi

Nooni99, 2024-04-30:
@wes4560 I found the solution. Since the chip is an RP2040, it will use boot mode. Your device should appear as "Raspberry Pi RP2 Boot" which is effectively the same as DFU mode. You can download firmware to it with no problem. Best of luck!

mprenter, 2024-06-15:
Same issue as everyone above, having a brand new board and unable to get it into DFU mode.  Can get the device to say "RP2 Boot" which some people say is good enough, but how do I install the firmware without using the dfu-util?

Nooni99, 2024-06-15:
@mprenter please don't make the misunderstanding I did. "RP2 Boot" is the "DFU mode" of this board. Since the board has a RP chip, it uses "RP2 Boot" instead. So follow all the steps you should follow and once you have "RP2 Boot" you're ready to move onto the next steps. You should be able to install the firmware the same you would any other chip. Let me know if you have more questions.

looxonline, 2024-06-15:
> Same issue as everyone above, having a brand new board and unable to get it into DFU mode. Can get the device to say "RP2 Boot" which some people say is good enough, but how do I install the firmware without using the dfu-util?

This is not an ST chip. It is an RP chip. You can't use dfu-util with it, you need to use the programming methods mentioned in the manual.

Destra-Slaybot, 2024-09-02:
> Have you found a solution @alexrizk1117 ? I am having the same issue except I see " Raspberry Pi RP2 Boot" when I try to go to DFU mode. Despite this, I am unable to enter dfu mode.

was this ever solved, i can't get past this one part

bigtreetech, 2024-09-02:
> > Have you found a solution @alexrizk1117 ? I am having the same issue except I see " Raspberry Pi RP2 Boot" when I try to go to DFU mode. Despite this, I am unable to enter dfu mode.
>
> was this ever solved, i can't get past this one part

If you see this, then it is in DFU. It is an RP2040. The manual has the info you need.

lunchbox2883, 2024-10-13:
Same situation here... Not getting the DFU mode but i am getting the PI RP2 boot. but getting the same error as @Charleslotto above when pushing through with the flash

Closed 2024-06-15.

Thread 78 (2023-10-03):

EBB SB2209 rp2040 - NEOPIXEL DOESNT WORK

bugalaws, 2023-10-03:
Hello, i have e ebb sb2240 rp2040 …all things work well , extruder, thermistor, fans etc..  only the neopixel doesnt work. I allready have tested the neopixel directly in my mks robin nano and works well..

Some times when start de printer at de first time the leds comes green but if i change the color or the intensity it powering off the leds and stay off until reboot the printer

I am using this setup:

[neopixel sb_leds]
pin: EBBCan:gpio16
chain_count: 3
color_order: GRBW

jjkrygsman, 2023-11-11:
Maybe try setting the initial colors:

#initial_RED: 0.0
#initial_GREEN: 0.0
#initial_BLUE: 0.0
#initial_WHITE: 0.0

It's been working fine for me.

jasonmacdonald, 2024-02-19:
Did oyu ever solve this. I'm having a similar issue of colors not working right and if I try to go pure white, everything just turns off.

Gardosen, 2024-02-25:
same issue here.

rgbs turn on with a bluish default color, but the entire config does not work. no control possible.
this is fucked up hardly in my opinion...

JKtech3D, 2024-02-25:
> same issue here.
>
> rgbs turn on with a bluish default color, but the entire config does not work. no control possible. this is fucked up hardly in my opinion...

post your neopixel config

Gardosen, 2024-02-25:
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

`[neopixel sb_leds]
pin: EBBCan:gpio16
chain_count: 3
color_order: GRB

[gcode_macro _sb_vars]
variable_colors: {
        'logo': { # Colors for logo states
            'busy': {'r': 0.4, 'g': 0.0, 'b': 0.0, 'w': 0.0},
            'cleaning': {'r': 0.0, 'g': 0.02, 'b': 0.5, 'w': 0.0},
            'calibrating_z': {'r': 0.8, 'g': 0., 'b': 0.35, 'w': 0.0},
            'heating': {'r': 0.3, 'g': 0.18, 'b': 0.0, 'w': 0.0},
            'homing': {'r': 0.0, 'g': 0.6, 'b': 0.2, 'w': 0.0},
            'leveling': {'r': 0.5, 'g': 0.1, 'b': 0.4, 'w': 0.0},
            'meshing': {'r': 0.2, 'g': 1.0, 'b': 0.0, 'w': 0.0},
            'off': {'r': 0.0, 'g': 0.0, 'b': 0.0, 'w': 0.0},
            'printing': {'r': 0.0, 'g': 0.0, 'b': 1.0, 'w': 1.0},
            'standby': {'r': 0.1, 'g': 0.0, 'b': 0.1, 'w': 0.1},
        },
        'nozzle': { # Colors for nozzle states
            'heating': {'r': 0.8, 'g': 0.35, 'b': 0.0, 'w':0.0},
            'off': {'r': 0.0, 'g': 0.0, 'b': 0.0, 'w': 0.0},
            'on': {'r': 1.0, 'g': 1.0, 'b': 1.0, 'w':1.0},
            'standby': {'r': 0.1, 'g': 0.0, 'b': 0.1, 'w':0.0},
        },
        'thermal': {
            'hot': {'r': 1.0, 'g': 0.0, 'b': 0.0, 'w': 0.0},
            'cold': {'r': 0.3, 'g': 0.0, 'b': 0.3, 'w': 0.0}
        }
    }
variable_logo_led_name:         "sb_leds"
variable_logo_idx:              "1"
variable_nozzle_led_name:       "sb_leds"
variable_nozzle_idx:            "2,3"
gcode:
    # This section is required.  Do Not Delete.

[gcode_macro _set_sb_leds]
gcode:
    {% set red = params.RED|default(0)|float %}
    {% set green = params.GREEN|default(0)|float %}
    {% set blue = params.BLUE|default(0)|float %}
    {% set white = params.WHITE|default(0)|float %}
    {% set led = params.LED|string %}
    {% set idx = (params.IDX|string).split(',') %}
    {% set transmit_last = params.TRANSMIT|default(1) %}

    {% for led_index in idx %}
        {% set transmit=transmit_last if loop.last else 0 %}
        set_led led={led} red={red} green={green} blue={blue} white={white} index={led_index} transmit={transmit}
    {% endfor %}

[gcode_macro _set_sb_leds_by_name]
gcode:
    {% set leds_name = params.LEDS %}
    {% set color_name = params.COLOR %}
    {% set color = printer["gcode_macro _sb_vars"].colors[leds_name][color_name] %}
    {% set led = printer["gcode_macro _sb_vars"][leds_name + "_led_name"] %}
    {% set idx = printer["gcode_macro _sb_vars"][leds_name + "_idx"] %}
    {% set transmit = params.TRANSMIT|default(1) %}

    _set_sb_leds led={led} red={color.r} green={color.g} blue={color.b} white={color.w} idx="{idx}" transmit={transmit}

[gcode_macro _set_logo_leds]
gcode:
    {% set red = params.RED|default(0)|float %}
    {% set green = params.GREEN|default(0)|float %}
    {% set blue = params.BLUE|default(0)|float %}
    {% set white = params.WHITE|default(0)|float %}
    {% set led = printer["gcode_macro _sb_vars"].logo_led_name %}
    {% set idx = printer["gcode_macro _sb_vars"].logo_idx %}
    {% set transmit=params.TRANSMIT|default(1) %}

    _set_sb_leds led={led} red={red} green={green} blue={blue} white={white} idx="{idx}" transmit={transmit}

[gcode_macro _set_nozzle_leds]
gcode:
    {% set red = params.RED|default(0)|float %}
    {% set green = params.GREEN|default(0)|float %}
    {% set blue = params.BLUE|default(0)|float %}
    {% set white = params.WHITE|default(0)|float %}
    {% set led = printer["gcode_macro _sb_vars"].nozzle_led_name %}
    {% set idx = printer["gcode_macro _sb_vars"].nozzle_idx %}
    {% set transmit=params.TRANSMIT|default(1) %}

    _set_sb_leds led={led} red={red} green={green} blue={blue} white={white} idx="{idx}" transmit={transmit}

[gcode_macro set_logo_leds_off]
gcode:
    {% set transmit=params.TRANSMIT|default(1) %}
    _set_logo_leds red=0 blue=0 green=0 white=0 transmit={transmit}

[gcode_macro set_nozzle_leds_on]
gcode:
    {% set transmit=params.TRANSMIT|default(1) %}
    _set_sb_leds_by_name leds="nozzle" color="on" transmit={transmit}

[gcode_macro set_nozzle_leds_off]
gcode:
    {% set transmit=params.TRANSMIT|default(1) %}
    _set_sb_leds_by_name leds="nozzle" color="off" transmit={transmit}

[gcode_macro status_off]
gcode:
    set_logo_leds_off transmit=0
    set_nozzle_leds_off

[gcode_macro status_ready]
gcode:
    _set_sb_leds_by_name leds="logo" color="standby" transmit=0
    _set_sb_leds_by_name leds="nozzle" color="standby" transmit=1

[gcode_macro status_busy]
gcode:
    _set_sb_leds_by_name leds="logo" color="busy" transmit=0
    set_nozzle_leds_on

[gcode_macro status_heating]
gcode:
    _set_sb_leds_by_name leds="logo" color="heating" transmit=0
    _set_sb_leds_by_name leds="nozzle" color="heating" transmit=1

[gcode_macro status_leveling]
gcode:
    _set_sb_leds_by_name leds="logo" color="leveling" transmit=0
    set_nozzle_leds_on

[gcode_macro status_homing]
gcode:
    _set_sb_leds_by_name leds="logo" color="homing" transmit=0
    set_nozzle_leds_on

[gcode_macro status_cleaning]
gcode:
    _set_sb_leds_by_name leds="logo" color="cleaning" transmit=0
    set_nozzle_leds_on

[gcode_macro status_meshing]
gcode:
    _set_sb_leds_by_name leds="logo" color="meshing" transmit=0
    set_nozzle_leds_on

[gcode_macro status_calibrating_z]
gcode:
    _set_sb_leds_by_name leds="logo" color="calibrating_z" transmit=0
    set_nozzle_leds_on

[gcode_macro status_printing]
gcode:
    _set_sb_leds_by_name leds="logo" color="printing" transmit=0
    set_nozzle_leds_on
`

Pitufo123, 2024-06-30:
Anyone figure this out?  I've tried connecting the signal line to the 4w fan pwm as well but no matter what I've tried can't get mine to work

mateusdemboski, 2024-08-01:
Same problem...

@bigtreetech could you help here?

Pitufo123, 2024-08-01:
In my case the problem ended up being faulty neopixels in my siboor kit.  Ordered a new string and they worked just fine

mateusdemboski, 2024-08-01:
I found a workaround on Reddit that resumes in use fan PWM pin instead of RGB pin. It worked for me.

bigtreetech, 2024-08-02:
The RGB pin is protected via a 100ohm resistor at the output. This ensures that the pin is not damaged if it is shorted to something that it should not be. If you have problems with a particular RGB strip then it could be that the strip has an input resistance that is too low on the signal line (it should be incredibly high so that there is no volt drop on a proper RGB strip). You could try to remove and short this resistor out if it is affecting you but it is important to know that you lose protection on that pin so don't short it. The resistor is R55

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

skyguy94, 2024-09-01:
@bigtreetech I can't find a document that tells you which resistor is R55, nor is there anything on the screen print of the SB0000 that indicates which is R55. The SMD components/board layout are tight enough that I'm having difficulty measuring the impedance of the resistors to determine which is the 10k and which is the 100 ohm.

The only references I can find of the SB0000 are in the build guide and the 3D PDF model. Can you post a picture with R55 labelled?

bigtreetech, 2024-09-03:
> The only references I can find of the SB0000 are in the build guide and the 3D PDF model. Can you post a picture with R55 labelled?

Here it is. Please let me know if it works out for you. It will be interesting if some RGB LED variants have been manufactured with very low input impedance.

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

skyguy94, 2024-09-06:
Ok, I removed the resistor and soldered a small piece of wire in its place and the neopixels did not turn on. Its fair to say that I could have damaged the pads, traces, or components and introduced a different problem, but I don't have a way of probing something this tightly packed to test. However, I did switch to my spare EBB2209 and EBB SB0000 those worked without an issue.

Pitufo123, 2024-09-29:
I'm having the exact same issue but this time it's not my neopixels I've got a brand new board.  Fair to assume it's faulty?  I read somewhere there's a batch of faulty boards on Amazon.

jchodakowski, 2024-09-29:
@Pitufo123 where did you source your new board and how much of the set did you replace?

Pitufo123, 2024-09-29:
I bought the board(s) off amazon as well as the neopixel chains. I tried only replacing the sb2208 board and theb also swapped out the 0000 daughter board.  Everything else works except for the neopixels.  And I've checked for broken wires on the neopixel chain.

Get Outlook for Android<https://aka.ms/AAb9ysg>

________________________________
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

tsoos99dev, 2025-01-08:
I have a similar issue. First, I burned out the Schmitt-trigger for the 4 wire fan input, and then I bent the main power input while testing the bed corner locations. I finished my first print at least, so I'll look into what's going on with the LEDs. I can't change their colour at all. I'll check the power and data pins tomorrow, and also verify that the LEDs are fine separately.

dutchronnie, 2025-01-12:
It was a faulty chip on the SB0000, i have replaced the chip for a new one,
and everything was working again

Op wo 8 jan 2025 om 23:28 schreef Soós Tamás ***@***.***>:

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

Dummykid, 2025-01-14:
well,
1st try: I bought brand new Bigtreetech SB LED light, and it didn't work.
2nd try: I bought brand new SB0000, and it didn't work.
3rd try: I removed the "yellow-signal" pin from the LED dupoint connector, and connected it to the fan PWM port and it worked.

I think BTT need to have quality control on its product. I have read all the posts here and everyone got different issue on this LED light.

sdylewski, 2025-02-02:
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

Which chip was this?  the SN74LVC1G17?

sdylewski, 2025-02-04:
I have the same problem, and tried shorting the resistor R55, but still doesn't work.  When I first connected my LED board, my lights worked, but stopped during the first print. Is it possible I have a faulty SN74LVC1G17?

dutchronnie, 2025-02-04:
Yes it was that chip,
[image: image.png]
Bought this one to replace: https://nl.aliexpress.com/i/32843534645.html

Op di 4 feb 2025 om 17:59 schreef Scott Dylewski ***@***.***>:

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

ptamarin, 2025-05-03:
Also having this issue with GPIO16 pin, just testing my neopixel leds (with raspberry pi 3b via its GPIO) and can rule them out. Leds and BTT SB2209 RP2040 from a formbot 2.4 kit

Closed 2024-08-02.

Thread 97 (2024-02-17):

BTT SKR3  EZ + EBB36 = not communicating

BazlTech, 2024-02-17:
I've followed the guides in this git repo, I've followed other guides in blog posts elsewhere.  Nothing I try actually makes this work.

Setup:
Raspi 4B running Klipper
BTT SKR3 EZ connected to Raspi via USB
BTT EBB 36 connected to SKR3 using CANBUS (CAN H to CAN H, CAN L to CAN L)

I've reflashed firmware to the SKR3 just to make sure I had the settings correct.  I've flashed CANBoot to the EBB36.  I've flashed Klipper to the EBB36, but nothing works.

For what it's worth, I've never been able to get this command to work:
~/klippy-env/bin/python ~/klipper/scripts/canbus_query.py can0

sntlewis, 2024-02-17:
two things (neither may apply to your case).  1) power to the EBB36?

2) While the PAD7 I run supposedly supports CANBUS, I never could get it to recognize the EBB36.  Added U2C and all was straight forward.

Like I said, neither may be helpful..

BazlTech, 2024-02-20:
I was able to determine the proper sequence of events to make this work.  BTT should really do a better job with their user manuals.  What made my issue more complicated was I already had a working system before integrating the EBB36.  Things may have been more obvious if I had started completed from scratch with all of the equipment at once.

Here is the short and sweet of it:

1. Flash the SKR 3 EZ with Klipper, but select the USB to CAN option (I think the CANBUS pins are PB8/PB9?).  I used the following method for this:  Rename klipper.bin to firmware.bin.  Copy file to microSD card. Insert into SKR.  Power up for 5 seconds, power down and remove SD card.
3. Flash the EBB36 with Klipper configured to run over CAN (PB0/PB1) using the USB-C connection (you'll need to use the jumper to select USB power).  **DO NOT DO THIS WITH THE SKR3 POWERED UP** if you have your EBB36 already connected to the SKR.
4. Connect CANBUS wiring from EBB36 to SKR 3 EZ.  Swap the jumper over to the 120R resistor position.
5. Power up the SKR.
6. Using your Pi (that is connected via USB to the SKR), you'll need to use the python command to view your CANBUS devices and grab their IDs.
7. Edit your printer.cfg file's MCU sections (main one for the SKR, the secondary "mcu EBBCan" section for the other CANBUS ID)
8. Restart firmware
9. PROFIT

Closed 2024-02-20.

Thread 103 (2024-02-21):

EBB2240  with PT1000 clarification

donmahallem, 2024-02-21:
I do have a question regarding the **EBB2240** boards. I do use a Rapido V2 hotend with a **TWO wire PT1000** Thermistor. While looking for something else in the [schematics](https://github.com/bigtreetech/EBB/blob/master/EBB%20SB2240_2209%20CAN/SB2240/Hardware/BIGTREETECH%20EBB%20SB2240%20CAN%20%20V1.0_SCH.pdf) I did notice that the board specifies a 4300R resistor while the Klipper [docs](https://www.klipper3d.org/Config_Reference.html#directly-connected-pt1000-sensor) specifies a 4700 Pullup resistor. Am I correct with my assumption that I do have to replace the 4700 default with the 4300? (I did set the dip switches to the PT1000 position before). I just want to make sure before I go ahead as this would mean a significantly higher temperature

Karl-Barx, 2025-02-13:
Did you ever figure this out I'm having a hell or a time with mine

donmahallem, 2025-02-13:
Can't look up the dip switches currently but I have this config running for several months unchanged:
```sensor_type:MAX31865
sensor_pin: EBBCan: PA4
spi_bus: spi1
rtd_nominal_r: 1000
rtd_reference_r: 4300
rtd_num_of_wires: 2```

bigtreetech, 2025-02-13:
The EBB2240 has a MAX. The user is running an EBB USB which does not. His config will be different.

Closed 2024-02-21.

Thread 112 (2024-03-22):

TACH on SB22** Boards does not work.

M3HNGRY, 2024-03-22:
The tach do no work on the SB2240 with 9200rpm 4wire 5015 fan. My slider works but rpm/tach doesn't change. 😦https://cdn.discordapp.com/attachments/1015253264935157861/1220590923080142868/image.png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

RED = 24v, Black is Ground, White = Tach and Blue PWM...
klipper v0.12.0-131-gd9043345

https://cdn.discordapp.com/attachments/1015253264935157861/1220592102321291334/image.png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

MattiaFontanaErrepinet, 2024-03-29:
Same problem on SB2209

chhe-01, 2024-04-11:
Hello, I think I might have the same problem. I use the SB2209 RP2040

B0rax, 2024-04-17:
For reference, this config works for me:
```
[fan]
pin: EBBCan: PB14
tachometer_pin: EBBCan: PB15
kick_start_time: 0.2
hardware_pwm: true
off_below: 0.3
```

christianhelbig, 2024-05-25:
> Hello, I had the same problem. Did you set the jumper on the V_4W-FAN? When I set it, the tacho worked for me.

Thank you so much! I had the same problem and this actually fixed it!

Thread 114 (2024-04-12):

SB2209/SB0000 Fans not working

brothereww, 2024-04-12:
After installing Klipper v12 everything thats connected to the SB0000 stopped working (Part/Hotend Fan and a Knomi Display).
The Hotend itself is Heating and the Thermistors are working too so i dont think its an issue on the SB2209 my guess is the SB0000 is not getting any current but im not really sure how/where to measure.
- I didnt change any wiring everything is as before the Update where everything worked just fine
- I didnt change anything in the cfg files (I did try to reverse the PA1 and PA0 in the cfg but it didnt work)
- I already replaced the SB0000 Board

Im running a Manta M8P Board with a CB1 and the SB2209 in USB Can Bridge Mode.
Everything else is working fine I also dont get any error reports.

dmradford, 2024-04-13:
I'm having the exact same issue. Manta M8P in usb-can bridge mode. Everything connected directly to the SB2209 (RP2040) board works correctly. I only have the standard 2 fans and RBG LED's connected to the SB0000, but I'm getting nothing. I assume the pinout is just wrong, but I've tried everything I can find.

brothereww, 2024-04-14:
I also have no clue what to do at this point but sure know as soon as it runs again im ditching the mysterybox that the voron is super pissed with this thing i have more hours in tinkering with this thing than it has print hours

anatolygor, 2024-06-04:
Same here. Did anyone resolve this issue?

brothereww, 2024-06-07:
I bought a new SB2209 and it worked again. I dont know what the issue with the old one was im sorry

qw3rtn, 2024-10-10:
Any news on this topic?

Everything works except for the fans on the SB0000 :/
SB2209 running in can bus mode.

marceneirojovem, 2024-11-20:
Same here with Neopixel led and Knomi 2

stokedgsxr, 2025-05-13:
> Any news on this topic?
>
> Everything works except for the fans on the SB0000 :/ SB2209 (RP2040) running in can bus mode.

Did you get this resolved?

qw3rtn, 2025-05-13:
> Did you get this resolved?

Not really. I bought another SB2209.
I guess I misaligned the pin header when putting all together and fried something on the SB2209 :(

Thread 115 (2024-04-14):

CAN Klipper reserved pin problem EBB36 / Manta E3EZ

cs301cs301, 2024-04-14:
I have the problem that some of the specified pins are already reserved for CAN. This means that I cannot use the ADXL cs_pin: EBBCan:PB12. Klipper gives error, is reserved for CAN. The E3EZ uses PB12 and PB13 for CAN communication.
I also cannot use the heater_pin: EBBCan:PB13, also reserved for CAN.
So can I not use CAN in this board combination?

Monra124, 2024-04-27:
I have the same problem, I have the ebb with usb communication plus the two power cables, when I turn it on it tells me that PIN PB13 is reserved for SPI2, have you found a solution?.

Thanks

cs301cs301, 2024-04-29:
> I have the same problem, I have the ebb with usb communication plus the two power cables, when I turn it on it tells me that PIN PB13 is reserved for SPI2, have you found a solution?.
>
> Thanks

I have now switched and use the CAN lines for USB. This works for the E3EZ + EBB36 combination. As for your problem, maybe a pin is named wrong? PB13 is actually the Heater pin on v1.2, SPI2 is PB12. Which boards are you using?

Monra124, 2024-04-30:
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

Exactly the same board, the E3EZ blanket.
With the fimrware installed from github.

Thanks for answering, I've also sent a ticket to BTT, let's see if they answer me

cs301cs301, 2024-04-30:
Then it can only be a config problem...
my configs:
[config-20240430-173109.zip](https://github.com/bigtreetech/EBB/files/15167182/config-20240430-173109.zip)
my menuconfigs:
E3EZ
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
EBB36
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

Firmware is Armbian 24.2.3 Bookworm with Linux 6.1.79-legacy-sun50iw9-btt

Monra124, 2024-04-30:
> Then it can only be a config problem... my configs: [config-20240430-173109.zip](https://github.com/bigtreetech/EBB/files/15167182/config-20240430-173109.zip) my menuconfigs: E3EZ ![E3EZ_menuconfig](https://private-user-images.githubusercontent.com/37987673/326878454-eb57118f-836b-4d9b-9dde-22fc7523d07f.jpg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) EBB36 ![EBB36_menuconfig](https://private-user-images.githubusercontent.com/37987673/326878465-7cf9a6a5-43e9-4222-ace0-1c9b2b4a43f1.jpg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)
>
> Firmware is Armbian 24.2.3 Bookworm with Linux 6.1.79-legacy-sun50iw9-btt

Thanks.
I have done this exactly the same, but when I enter the ebb input I get the PIN error PB13 reserved SPI2

Monra124, 2024-04-30:
I put an older version of the EBB CAN frimware, the error did not come out, I asked to update, it updates everything but the EBB, I downloaded the latest firmware_usb.bin version from the official repository and nothing.

What version of the EBB mcu do you have??

I currently have:
Your Klipper version is: v0.12.0-177-gaf149b47-dirty
MCU(s) which should be updated:
mcu: Current version v0.12.0-177-gaf149b47
EBBCan: Current version v0.12.0-9-gbb4711c5d

Monra124, 2024-04-30:
I updated the firm from menuconfig and the same error comes up again:
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

With the configuration:
[https://private-user-images.githubusercontent.com/37987673/326878465-7cf9a6a5-43e9-4222-ace0-1c9b2b4a43f1.jpg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](url)

cs301cs301, 2024-04-30:
It seems that you still have the old "fire-hazardous" v1.0 of EBB36. PB13 is there for SPI2.

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
For the heater you have to use PB1 in the config.

This is no longer the case with the new v1.2.

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

Monra124, 2024-04-30:
The ebb 36 can is v1.2.

The firm I install is the one they have on github v1.1 since it is the same as v1.2.

You won't have the firm you installed on yours to see if that's the problem.

Thank you very much for your time, I really appreciate it as I can't get it to work.

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

cs301cs301, 2024-04-30:
That's right, I did not use the pre-built firmware. I followed the instructions for Canboot (now Katapult).

https://wiki.kb-3d.com/en/home/btt/voron/BTT_EBB36

Monra124, 2024-04-30:
Ok, so you have it connected by CAN, instead of USB?

cs301cs301, 2024-04-30:
No, as I said, I use USB. (https://lab4450.com/latest-projects/upgrade-can-ebb36-to-usb-toolhead/)
Initially yes, but that didn't work. I then flashed Klipper over it with USB settings. I just don't know whether any of the old firmware remains on it, because sometimes you specify a bootloader offset, sometimes not.
I don't really know why it doesn't work for you.
Have you also rebuilt and flashed Klipper for the EBB36 or is it still running the firmware from github? The E3EZ board sees the EBB, so you can simply flash Klipper in DFU moder there and don't need the finished firmware.

Monra124, 2024-04-30:
The board sees the EBB36.
I've tried building the firmware, I've even tried installing RATOS from its installer and the same thing always ends up happening to me, it's as if you always give me a v1.0 signature.

I will take a look at the information you have given me, thank you very much

Monra124, 2024-05-01:
Good morning.
There is no way, no matter what I do the same result, I built the firmware and flashed it in dfu mode, it did it correctly, the result is the same, it's like you always build with the v1.0 board pins.

cs301cs301, 2024-05-01:
Can you pls upload your Klipper configs for EBB & E3EZ?

Monra124, 2024-05-01:
> Can you pls upload your Klipper configs for EBB & E3EZ?

I don't have everything done, as I first tried to link the E3EZ board with the EBB and then connect everything and finish the printer with its macros...

cs301cs301, 2024-05-01:
That's crazy, there is no double reference to PB13, so where is this error message coming from?
Just out of interest, have you tried entering PB1 for the heater instead of PB13? Not that it would work, but just to see if other error messages appear.

cs301cs301, 2024-05-01:
However, it appears that the board is faulty. Do you have the option of returning it?

Monra124, 2024-05-02:
I opened a ticket on the official BTT website where I bought it, but they don't answer

nexus665, 2024-08-28:
Hi,
I have the same problem - though I am using the EBB36 v1.2 with CAN (self-configured katapult bootloader, not precompiled binary).

As soon as I try to setup the ADXL345, it tells me that PB13 is reserved for spi2 and it cannot start. As above, I have only one reference to PB13, as in:

`[heater extruder]heater_pin: EBB36:PB13
`

`[adxl345]
cs_pin: EBB36:PB12
`

Only when I comment out the adxl section will Klipper start and connect.

Otherwise, it gives the exact same error message of:
`Pin PB13 is reserved for spi2`

Monra124, 2024-08-28:
Good morning, my problem was a faulty board, with its replacement it was easier to solve.

duder56, 2024-09-13:
> Good morning, my problem was a faulty board, with its replacement it was easier to solve.

when you say "faulty board" do you mean your main board, u2c, ebb36?

I have a Manta m8p v1.0, u2c v2.1, and ebb2240 and I'm getting the same error. I don't really see how a new board will fix this issue, as it would be in the coding?. The heater pin will always be PB13 for the heater, as this is how it appears in their schematics. I've tried starting from scratch twice now, it only worked the first install for about 10 min before the first reboot, then all I have been getting afterwards is the PB13 reserved problem. Quite frustrating that using all BTT products, would leave me without a working system...

Monra124, 2024-09-13:
If it was the defective EBB36, I don't know why.

I couldn't tell you, just check that the firmware you introduce is the right one.

duder56, 2024-09-13:
> If it was the defective EBB36, I don't know why.
>
> I couldn't tell you, just check that the firmware you introduce is the right one.

Ok thanks, at least that is the cheaper board to replace 😅

I've definitely made sure to have all the correct firmware, as it did work temporarily the first install. Then nothing was touched, aside from a reboot, and will not work. I've even gone as far as trying older firmware with fresh installs, and different issues arose with no communication to EBB bus, or the same pin error.

But I will try a new EBB board, thank you for the advice.

nexus665, 2024-09-13:
Hi duder,

did you try the solution I posted a couple of messages above, enabling Software SPI instead of Hardware SPI by defining the

spi_software_sclk_pin: EBBCan:PB10
spi_software_mosi_pin: EBBCan:PB11
spi_software_miso_pin: EBBCan:PB2

not just

cs_pin: EBBCan:PB12

on its own? Worked for me...

Of course, you could have a defective board, but hey, worth a try before you buy a new one...

Regards

Monra124, 2024-09-13:
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

I'm sorry I can't help you more.
I hope you fix it

duder56, 2024-09-13:
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

I have a EBB SB2240, and in the sample CFG this is how it is written already. But thank you for the suggestion, obviously I would also like to try all avenues before buying a new board 🤭

duder56, 2024-12-02:
Turns out my issue was stupidity. I had commented out the SPI's under the 2204 driver header, thinking I wasn't running SPI mode, because my 2209 drivers are not in SPI mode 🤦🏻 uncommenting these got ride of my SPI error.

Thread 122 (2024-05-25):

Jumper Pin

acozad1, 2024-05-25:
So I have lost the jumper pins for the fan voltage. Does anybody know where and size of those jumper pins?

Thank you for your hlep

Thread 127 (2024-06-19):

EBB36 v1.2 MAX31865 RTD input is disconnected

grigi, 2024-06-19:
Hi, Trying to configure my EBB36 v1.2 to use the MAX31865 for a 2-wire PT1000 sensor I get the following errors in my `klippy.log`:
```
Max31865 RTD input is disconnected
Max31865 RTD input is shorted
Max31865 VREF- is greater than 0.85 * VBIAS, FORCE- open
Max31865 VREF- is less than 0.85 * VBIAS, FORCE- open
Max31865 VRTD- is less than 0.85 * VBIAS, FORCE- open
Max31865 Overvoltage or undervoltage fault
```
Doing some research I found that this tends to indicate a wiring fault.

I manually tested the resistance and it's working fine, quadruple-checked that the dip switches are correct and that it's connected to the correct pins, but nothing would fix it.

Then I took a close look at the board, and saw this:
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

That ain't right?

grigi, 2024-06-19:
I re-soldered those components (They are tiny) and it resolved the issue.
I suspect they are too close to the mount point and was put under tension.

I modified my mount to leave more clearance at the bottom there so as to not apply tension on those components again.

A longer term solution would be to move those components further away from the screw hole, as this seems to be a relatively common issue.

looxonline, 2024-06-19:
Yea, looking at how they are both angled in a mirrored fashion suggests that whatever screw you put in there somehow pushed them out. Careful with that because it can rip the pads off the board. Glad that you got it sorted out though.

Closed 2024-06-19.

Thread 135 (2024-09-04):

Sb2209 usb v1 no boot mode

aee74, 2024-09-04:
I’ve tried to hold down boot press reset and let go of boot but no change when I loom at lsusb

how to get into boot mode. Is the board defective?

Aibehn, 2024-09-10:
I'm having the same problem.
- I supplied 24v to the adapter board, connected USB-C to RPi Host.
- Connected XT30(2+2) to both ends.
- Power led indicator goes ON. and a big STATUS led goes on RED.
- I hold press BOOT bottom, press & release RST buttom and after that I release the BOOT bottom.
STATUS led goes  off. POWER led still fine.
It should be on DFU now, but I don't see it with lsusb, or dfu-util -l

looxonline, 2024-09-10:
Could you both list your lsusb results before and after the process?

Aibehn, 2024-09-10:
> Could you both list your lsusb results before and after the process?

`Bus 002 Device 001: ID 1d6b:0003 Linux Foundation 3.0 root hub
Bus 001 Device 007: ID 1d50:614e OpenMoko, Inc. stm32h743xx
Bus 001 Device 002: ID 2109:3431 VIA Labs, Inc. Hub
Bus 001 Device 001: ID 1d6b:0002 Linux Foundation 2.0 root hub`

No changes.

looxonline, 2024-09-10:
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

That lsusb is before or after going into boot mode or is there zero difference between the two?

Aibehn, 2024-09-10:
``

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

ZERO difference

looxonline, 2024-09-10:
Also what USB-C cable are you using between the SBC and the adapter PCB? Is it the one supplied with the part or your own? Have you tried using other cables?

Aibehn, 2024-09-10:
> Also what USB-C cable are you using between the SBC and the adapter PCB? Is it the one supplied with the part or your own? Have you tried using other cables?

I'm using the one supplied. But I did also test a different usb-c to usb-a cable. Same results.

looxonline, 2024-09-10:
OK, fire off an email to luke@bigtree-tech.com and I'll ask the support team to look deeper into your case.

Aibehn, 2024-09-11:
Just a quick update because things escalated quickly.

I was testing it with another host, an RPi2B that I had lying around. At first, no changes, just the same result: no way to get it into DFU mode or recognized by the RPi.

At first, it seemed that the RPi was having power problems. I noticed that plugging in the USB-C cable would cause the power status LED on the RPi to flicker. But then it got worse.

I tried another USB-C cable, and at first, nothing seemed to happen—everything was fine, no magic smoke. After that, it started to smell, and I noticed that the SB2209 was getting hot. Still, no lsusb device, and the status LED was fine.

I tried one more time with the boot/rst button combo, and the LEDs just went off—no magic smoke, nothing. Then I noticed the RPi power LED going crazy. The SMSC chip controller (USB hub & LAN) was getting extremely hot. I disconnected everything, but it was too late.

The RPi2B doesn't boot anymore. The USB hub controller chip gets extremely hot.

The SB2209 doesn't show any LED status anymore. It gets 24V through the adapter board, but nothing happens. No heated components either.

At least It was not the RPi4 and a RPi2B that died. I not hooking anything without a USB isolator or something similar.

tl;dr: SB2209 died and It killed a RPi2B on the process.

looxonline, 2024-09-11:
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

Please take the exact connection that you have, remove the EBB USB from one end and the Pi from the other and measure to see if the data pins are shorting to any of the power pins or each other.

anilfrace, 2025-01-07:
Has anybody solved this issue?
I am facing exactly the same issue, can somebody guideline me to solve it?

jace, 2025-01-27:
I have a new SB2209 USB and it refused to go into bootloader mode, same as the other reports here. After a couple attempts at boot+reset however, it showed up in `lsusb` and in `/dev/serial/by-id`:

```
Bus 001 Device 016: ID 1d50:614e OpenMoko, Inc. rp2040
```
I then tried to flash it directly using `make flash FLASH_DEVICE=/dev/serial/by-id/usb-Klipper_rp2040_xxxxxxx` but that failed:

```
  Flashing out/klipper.uf2 to /dev/serial/by-id/usb-Klipper_rp2040_xxxxx
Entering bootloader on /dev/serial/by-id/usb-Klipper_rp2040_xxxxx
Device reconnect on /sys/devices/platform/scb/fd500000.pcie/pci0000:00/0000:00:00.0/0000:01:00.0/usb1/1-1/1-1.4/1-1.4.4/busnum
Traceback (most recent call last):
  File "/home/pi/klipper/./scripts/flash_usb.py", line 390, in <module>
    main()
  File "/home/pi/klipper/./scripts/flash_usb.py", line 387, in main
    flash_func(options, args[0])
  File "/home/pi/klipper/./scripts/flash_usb.py", line 340, in flash_rp2040
    flash_picoboot(options.device, binfile, options.sudo)
  File "/home/pi/klipper/./scripts/flash_usb.py", line 202, in flash_picoboot
    with open(usbdir + "/busnum") as f:
FileNotFoundError: [Errno 2] No such file or directory: '/sys/devices/platform/scb/fd500000.pcie/pci0000:00/0000:00:00.0/0000:01:00.0/usb1/1-1/1-1.4/1-1.4.4/busnum'
make: *** [src/rp2040/Makefile:78: flash] Error 1
```

Instead, it _now_ showed up in bootloader mode in `lsusb` and I was then able to flash it with `make flash FLASH_DEVICE=2e8a:0003`. Now it works.

jace, 2025-01-27:
I gave my board a test-run by turning the hotend up to 150°C. It worked for about a minute and then shutdown. The board no longer shows up in `lsusb`, even after a few power cycles. I changed the USB cable to a known-good cable but that didn't help either. The LED on the board no longer changes color/intensity when I press boot+reset.

Looks like I have a dead board too?

jace, 2025-02-01:
Turns out I have a bad cable with a loose contact in one of the plugs, so I sliced it open to inspect:

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

I'm not an electronics professional, but is that solder on crimped wires? Doesn't that make it brittle and prone to damage like this? And is that shielding sleeve on the middle neutral wire electrically conductive? It's got strands sticking out dangerously close to the 24V wire.

looxonline, 2025-02-01:
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

There is no crimping. The XT30 connectors are entirely soldered. The internals are potted with glue to prevent the shielding from touching surrounding wires.

jace, 2025-02-04:
You're right. I got a spare XT30 2+2 plug and that takes crimped leads, but the SB2209 USB cable is just soldered. The spare has lock holes for crimped leads.

I've resoldered and hot glued the leads on mine and it's now working. Hope this holds until there's a replacement.

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

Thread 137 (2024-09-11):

rp2040 will not go into DFU Mode

Charleslotto, 2024-09-11:
I have all connections disconnected except USB. did the hold boot and unplug/plug in the usb cable and still nothing.

I see below and get an error:
biqu@BTT-CB1:~/klipper$ lsusb
Bus 008 Device 001: ID 1d6b:0001 Linux Foundation 1.1 root hub
Bus 004 Device 001: ID 1d6b:0002 Linux Foundation 2.0 root hub
Bus 007 Device 001: ID 1d6b:0001 Linux Foundation 1.1 root hub
Bus 003 Device 001: ID 1d6b:0002 Linux Foundation 2.0 root hub
Bus 006 Device 001: ID 1d6b:0001 Linux Foundation 1.1 root hub
Bus 002 Device 004: ID 1d50:614e OpenMoko, Inc. stm32g0b1xx
Bus 002 Device 015: ID 2e8a:0003 Raspberry Pi RP2 Boot
Bus 002 Device 003: ID 04d9:8030 Holtek Semiconductor, Inc. BTT-HDMI5
Bus 002 Device 002: ID 1a40:0101 Terminus Technology Inc. Hub
Bus 002 Device 001: ID 1d6b:0002 Linux Foundation 2.0 root hub
Bus 005 Device 001: ID 1d6b:0001 Linux Foundation 1.1 root hub
Bus 001 Device 001: ID 1d6b:0002 Linux Foundation 2.0 root hub
biqu@BTT-CB1:~/klipper$ make flash FLASH_DEVICE=2e8a:0003
Flashing out/klipper.bin to 2e8a:0003
sudo dfu-util -d ,2e8a:0003 -R -a 0 -s 0x8000000:leave -D out/klipper.bin

dfu-util 0.9

Copyright 2005-2009 Weston Schmidt, Harald Welte and OpenMoko Inc.
Copyright 2010-2016 Tormod Volden and Stefan Schmidt
This program is Free Software and has ABSOLUTELY NO WARRANTY
Please report bugs to http://sourceforge.net/p/dfu-util/tickets/

dfu-util: Invalid DFU suffix signature
dfu-util: A valid DFU suffix will be required in a future dfu-util release!!!
dfu-util: No DFU capable USB device available

Failed to flash to 2e8a:0003: Error running dfu-util

If the device is already in bootloader mode it can be flashed with the
following command:
make flash FLASH_DEVICE=0483:df11
OR
make flash FLASH_DEVICE=1209:beba

If attempting to flash via 3.3V serial, then use:
make serialflash FLASH_DEVICE=2e8a:0003

make: *** [src/stm32/Makefile:111: flash] Error 255

looxonline, 2024-09-11:
dfu-util is a tool for STM microcontrollers and will not work with RP2040 microcontrollers. Please follow the respective product manual for different programming options based on the MCU type.

Charleslotto, 2024-09-11:
I guess I didn't describe it right, I am trying to do the Canbus SB2240 and SB2209 setup but get to the flashing of SB2240 when I put it in what should be DFU mode it shows up as 2e8a:0003 Raspberry Pi RP2 Boot or 1d50:614e OpenMoko, Inc. rp2040 when I just power it on.

looxonline, 2024-09-11:
The SB2209 and SB2240 (non RP2040 variants) are using STM chips. The address you therefore want to use with DFU util is: 1d50:614e OpenMoko, Inc. stm32g0b1xx

Closed 2024-09-11.

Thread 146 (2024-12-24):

SB0000 fans not working

SunayKichukov, 2024-12-24:
I have seen this somewhere with other users having the same issue, the fans connected to the SB0000 just don't run
can somebody address this issue because I spend 2 days taring to find the error but it seams to be the either of the SB000 board or the EBB SB2209.

bigtreetech, 2024-12-24:
Please make sure that you have a proper connection between the main board and the SB0000. Often users have a pin offset or the pins are not reaching deep enough into the main board. Check your pin offset and then also apply pressure to the front of the stealth burner with one of the fans turned on to see if that starts it spinning. Over tightening the bottom screws on the stealth burner can cause this bad connection.

SunayKichukov, 2024-12-24:
I have tested the connections and I ordered another SB0000 just to see if the board is the problem. Unfortunately they both behave the same. I have Heater, extruder motor, BLtouch and a pt1000 sensor hooked to the SB2209 and they all work. The part cooling fan runs at max voltage at whatever power the jumper is set at and the heatsink fan doesn't run at all. I checked the wiring and the pinout only 20 times so I believe that is not the problem, The pinout is set as follows:

[fan]
pin: EBBCan: PA1

[heater_fan hotend_fan]
pin: EBBCan: PA0
max_power: 1.0
fan_speed: 1
kick_start_time: 0.1
heater: extruder
heater_temp: 30.0

The main board is octopus MAX EZ
running on BTT pi v2

bigtreetech, 2024-12-24:
The SB2209 simply outputs PWM signals directly from the microcontroller to the MOSFETS on the SB0000. If the SB0000 was inserted with incorrect pin alignment or inserted/removed with the power to the machine on at any point then it is possible to cause damage to these pins on the MCU and that may result in fans either staying on permanently or not turning on at all. It is best to contact our support team using the ticketing system on the website as github is not one of our official support channels. It is mostly used as a means for engineers to interact with customers when gathering product feedback.

Closed 2024-12-24.

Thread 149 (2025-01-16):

SB2209 RP2040 MCU 'EBBCan' shutdown: Thermocouple reader fault (SOLVED)

mylastregret, 2025-01-16:
[extruder]
step_pin: EBBCan:gpio18
dir_pin: !EBBCan:gpio19
enable_pin: !EBBCan:gpio17
rotation_distance: 22.6789511   #Bondtech 5mm Drive Gears

gear_ratio: 50:10
microsteps: 16
full_steps_per_rotation: 200	#200 for 1.8 degree, 400 for 0.9 degree
nozzle_diameter: 0.400
filament_diameter: 1.75
heater_pin: EBBCan:gpio7

sensor_type: MAX31865
sensor_pin: EBBCan:gpio9
spi_software_sclk_pin: EBBCan:gpio10
spi_software_mosi_pin: EBBCan:gpio8
spi_software_miso_pin: EBBCan:gpio11
min_temp: 10
max_temp: 270
max_power: 1.0
min_extrude_temp: 170
rtd_nominal_r: 1000
rtd_reference_r: 4300
rtd_num_of_wires: 2
control = pid
pid_kp = 26.213
pid_ki = 1.304
pid_kd = 131.721

CharlesNoScreen, 2025-02-03:
How did you solve it?

kingbob2, 2025-03-03:
same issue. solution? I'm suspecting bad physical connection.

mylastregret, 2025-03-05:
Are you using a PT1000 or PT100?

kingbob2, 2025-03-05:
PT1000. It was indeed a bad physical connection. Tore my stealthburner hotend down and found I pinched a thermistor wire.

Closed 2025-02-18.

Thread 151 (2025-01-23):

Main Body and Cable Cover for SB2209 RP2040 Version?

CookiezRGood, 2025-01-23:
I can't find files for the different stealthburner body and cable cover to fit this board in my toolhead. I tried printing the one for the SB2209 since that section has STL files but it doesn't fit. The PDF for assembly shows a different cable cover model but I can't find the file anywhere.

phenolplus, 2025-02-25:
Same issue. [Cable_Cover_EBB.stl](https://github.com/bigtreetech/EBB/blob/master/EBB%20SB2240_2209%20CAN/STL/Cable_Cover_EBB.stl) is very tight on the top. It's pinching the probe wires when one is plugged in.

CookiezRGood, 2025-02-25:
I actually modified my own version in Blender to make it fit and it works great. I just grabbed all the middle points and extended them out a bit while leaving the edges the same so it still lines up with the body they provide. I uploaded it to Thingiverse and have the link below.

https://www.thingiverse.com/thing:6961699

Closed 2025-02-25.

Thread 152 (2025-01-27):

SB2209 USB and PT1000 thermistor

jace, 2025-01-27:
I have a PT1000 sensor in my Rapido Hotend 2, which I've connected to the TH0 port of SB2209 USB, with the switch pushed up to `PT` side. My Klipper is configured as per the example config:

```ini
[extruder]
pullup_resistor: 2200 # 2.2K
sensor_type: PT1000
sensor_pin: EBB:gpio26
```

However, Klipper fails to start reporting ADC out of range (21000+°C). If I remove `pullup_resistor`, it goes even higher. What is the correct setting for PT1000?

jace, 2025-01-27:
Resolved by pushing the switch down to the NTC side. Now it reports temperature correctly. However, the board has shutdown entirely after a few minutes and no longer shows up as a USB device (similar reports in #135).

Please fix the documentation on PT1000 vs NTC as the diagrams in the manual and on the board are not clear at all. Is this supposed to mean I have to select NTC even for PT1000? What is the purpose of the switch then?

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

jace, 2025-01-27:
I think I understand now:

If the switch is set to PT, it requires the MAX31865 chip and the additional switches (PT100 or PT1000) to be soldered onto the board, as shown in the bottom right corner of the image. Without them, it's just cutting off the signal.

Leaving this comment here for the next person who's similarly confused.

Karl-Barx, 2025-02-13:
What was your solution for this? I'm about to ditch the pt1000 on my rapido for an ntc but really don't want to since it will require redoing my faceplate for sb. Any help is greatly appreciated!

Karl-Barx, 2025-02-13:
I'm just very confused since the market the sb2209 as being pt1000, give you almost no information, and then leave you out to dry. Very frustrating

bigtreetech, 2025-02-13:
The manual contains all of the instructions. Set the switch to NTC and then configure the PT1000 within klipper.

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

Karl-Barx, 2025-02-13:
You should check you discord. I'm not the only one with this issue. I've heard from multiple people that you must solder a switch and max chip to get it working. Is this true?

bigtreetech, 2025-02-13:
No, it's not true. You just plug it in, follow the manual guidance on what to set the switch to and configure klipper for a PT1000 thermistor with a 2k2 pull up.

Closed 2025-01-27.

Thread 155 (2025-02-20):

USB Errors when homing with SB2209 USB

keyz182, 2025-02-20:
When homing Z, as soon as the head reaches the X/Y coords, this error is shown in the output from `dmesg` corresponding to the SB2209 hub

```
[  851.124515] usb 1-3: clear tt 1 (91b1) error -71
[  851.124719] usb 1-3: clear tt 1 (91b1) error -71
[  851.124992] usb 1-3: clear tt 1 (91b1) error -71
[  851.125473] usb 1-3: clear tt 1 (91b1) error -71
[  851.125655] usb 1-3: clear tt 1 (91b1) error -71
[  851.125946] usb 1-3: clear tt 1 (91b1) error -71
[  851.126346] usb 1-3: clear tt 1 (91b1) error -71
[  851.126403] usb 1-3: USB disconnect, device number 19
[  851.126410] usb 1-3.4: USB disconnect, device number 20
[  851.380032] usb 1-3: new full-speed USB device number 23 using xhci_hcd
[  851.495156] usb 1-3: device descriptor read/64, error -71
[  851.712069] usb 1-3: device descriptor read/64, error -71
[  851.935038] usb 1-3: new full-speed USB device number 24 using xhci_hcd
[  852.051918] usb 1-3: device descriptor read/64, error -71
[  852.271289] usb 1-3: device descriptor read/64, error -71
[  852.373998] usb usb1-port3: attempt power cycle
[  852.760990] usb 1-3: new full-speed USB device number 25 using xhci_hcd
[  852.761127] usb 1-3: Device not responding to setup address.
[  852.965096] usb 1-3: Device not responding to setup address.
[  853.172869] usb 1-3: device not accepting address 25, error -71
[  853.172989] usb 1-3: WARN: invalid context state for evaluate context command.
[  853.286857] usb 1-3: new full-speed USB device number 26 using xhci_hcd
[  853.287025] usb 1-3: Device not responding to setup address.
[  853.493078] usb 1-3: Device not responding to setup address.
[  853.700841] usb 1-3: device not accepting address 26, error -71
[  853.700972] usb 1-3: WARN: invalid context state for evaluate context command.
[  853.701108] usb usb1-port3: unable to enumerate USB device
```

And these logs from klippy.log - https://gist.github.com/keyz182/8b07d0463c88b53338cec88a898f6e0a
I've tried it on different ports on the computer with no luck.

I did have a Beacon3D RevH and a 3DO V2 camera plugged in - for testing I have removed the camera, and wired the Beacon in a separate cable rather than through the SB2209 USB hub to eliminate variables. Still the same result with no USB devices plugged into the SB2209.

I am using the supplied cable from the SB2209, and have installed the grounding wire.

bigtreetech, 2025-02-20:
It may be cable related. Could you try to wrap a small cable tie around the connector like this and see if it makes a difference? Sometimes the cable moves within the socket and causes microsecond disconnects.

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

keyz182, 2025-02-20:
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

This is about the best I could manage, but it still errors out.

keyz182, 2025-02-20:
Even tried a small dab of glue to try to hold it in place better (second photo you can see it). No luck

keyz182, 2025-02-20:
I think the cable might be damaged. I can't get it to connect at all now - just that same error in `dmesg` each time I unplug/plug in, even after taking the cable out of the chain.

keyz182, 2025-02-22:
Confirmed the cable is bad - no continuity on the DP line. Must have been small enough a break that it worked for a while then slowly moved apart until there's no contact at all now. Will get a new cable.

keyz182, 2025-02-22:
Different cable, same error, so I must have just badly meaured the old one or something. An LDO Nitehawk connects and works correctly over this cable if I swap it over. So I guess it must be board related?

andzymonek, 2025-02-28:
https://github.com/bigtreetech/EBB/issues/157

check the quality of the solders, you can see that there is a bigger problem with it

keyz182, 2025-02-28:
@andzymonek I did reflow those joints, to no avail unfortunately. I've contacted support as I suspect something on the board is dead. My guess is the circuitry driving the onboard USB hub, or the usb hub chip itself. Total guess though.

Closed 2025-03-20.

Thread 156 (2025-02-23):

Pinheader Type EBB SB2209

Battlecake91, 2025-02-23:
I broke my pinheader from the Main PCB of the SB to the Fan-Breakout. I cannot find any possible Pinheaders. I tried some I have at home, but they don't fit as the original pinheaders have 0.5mm diameter and normal square ones have 0.64mm.
I tried then one that fits with 0.64mm but it is too long and now nothing fits.

Does anyone now what part is used original?

Johnnytk36, 2025-04-04:
The generic name is Dunpont 2.0mm spacing. Though in my research they could be a knockoff of molex MilliGrid connectors also.

I know because I wanted to make a male to female jumper to do some testing on y fan board related to the tach line feedback.

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

You could get the connector here. [2.0mm Double Row Right Angle Pin Header Strip Male Pin Copper Needle Nickel Plated](https://www.aliexpress.us/item/3256802252624530.html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)

Battlecake91, 2025-04-04:
Thanks for your reply, but I'm sure it is 2,54mm.

Also the problem is, that the linked pinheader doesn't fit because of the length of the pins. I had some and tried to connect it with them, but you cannot put on the cover completelly after doing this.

Johnnytk36, 2025-04-04:
That's weird. Yeah, i don't know which one you have then. As the spec sheets show 14 pins like the one i have.  The making board SB0000 is the same for the SB2209 and SB2240 it shows also.

[BIGTREETECHEBB SB2209 CAN V1.0_IO.pdf](https://github.com/user-attachments/files/19607779/BIGTREETECHEBB.SB2209.CAN.V1.0_IO.pdf)

[BIGTREETECH EBB SB0000 CAN V1.0_size.pdf](https://github.com/user-attachments/files/19607806/BIGTREETECH.EBB.SB0000.CAN.V1.0_size.pdf)

Johnnytk36, 2025-04-04:
Nevermind found it. I haven't updated my files on my laptop in a while, and i didnt show the have the files for the SB2209 USB version. The USB version has 10 pins.

[BIGTREETECH EBB SB2209 USB-Pin.pdf](https://github.com/user-attachments/files/19607849/BIGTREETECH.EBB.SB2209.USB-Pin.pdf)

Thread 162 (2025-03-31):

Pi does not boot when the SB2209 is plugged in

cmeyer231, 2025-03-31:
Pi does not boot when the SB2209 is plugged in, but once I unplug the SB2209, either with the USB C or the XT30 it boots fine. I can plug the USB in right away and nothing seems to be wrong, the board and PI operate 100% normally.

I have tried Kapton tape over the 5V pin on the PI side of the USB cable, different USB cables and the same issue occurs.

This was a replacement for the previous SB2209 I had that kept getting "timer too close" errors. This replacement seems to have fixed that problem but now the PI booting issue is now.

I though wiring on the hot end side might be bad, but the board causes the issue without anything plugged in at all other than the XT30.

Compared to the random TTC errors causing the print to stop 2-3 hours in this a a more minor frustration, but still would like to get it fixed.

Pi being powered from my Spider 2.2 board and a separate 24 to 5v buck converter (both rated at 3 amps) - same issue.

asyncmeow, 2025-04-13:
saw this issue while checking to see if someone asked another here about something i was wondering and saw this. after having a similar issue with my Octopus Pro board earlier - what model pi are you on? the 4b has an issue where if power is getting backfed from a USB port, it doesn't boot. i was able to resolve this earlier by adding a USB hub in-between the pi and board, but one way you might be able to check is by connecting the pi to a display while it's booting - when you power up the pi, does it reach the firmware of the pi before you unplug the SB2209? or is it stopping later on in the boot process?

for context, here's a video of the issue i had - does your issue look similar?:

https://github.com/user-attachments/assets/ecaee532-677a-40af-8ea5-bd75c6dc929d

cmeyer231, 2025-04-13:
It is exactly the same as what I have. Noting happens on screen until the toolhead is unplugged.

I thought it was power backed as well, so only the data lines are connected. I used kapton tape on the pins, and verified there was no voltage on the USB c side when properly powered.

I can also unplug the board from the toolhead side and it boots, so it definitely seems like something with the data lines, since power would still be backfed in that case.

A USB hub controller between the two would make sense if there is something the rpi is doing that is breaking it. I may try and use an old version of klipper and see if there is a bug introduced in a recent version.

asyncmeow, 2025-04-13:
the thing that makes me unsure if it's a klipper specific issue is that i have other boards running klipper that i can leave plugged in while it's booting without issue, but something with the data lines could be another explanation for it - just not sure how to debug it... i have a usb packet analyzer somewhere, but no way to run its software anymore (or the cables i need for it) and its usb1.1 only so i am unsure if it would help here 😅On Apr 13, 2025 11:49, cmeyer231 ***@***.***> wrote:
  It is exactly the same as what I have. Noting happens on screen until the toolhead is unplugged.
I thought it was power backed as well, so only the data lines are connected. I used kapton tape on the pins, and verified there was no voltage on the USB c side when properly powered.
I can also unplug the board from the toolhead side and it boots, so it definitely seems like something with the data lines, since power would still be backfed in that case.
A USB hub controller between the two would make sense if there is something the rpi is doing that is breaking it. I may try and use an old version of klipper and see if there is a bug introduced in a recent version.—Reply to this email directly, view it on GitHub, or unsubscribe.You are receiving this because you commented.Message ID: ***@***.***>

cmeyer231 left a comment (bigtreetech/EBB#162)
It is exactly the same as what I have. Noting happens on screen until the toolhead is unplugged.
I thought it was power backed as well, so only the data lines are connected. I used kapton tape on the pins, and verified there was no voltage on the USB c side when properly powered.
I can also unplug the board from the toolhead side and it boots, so it definitely seems like something with the data lines, since power would still be backfed in that case.
A USB hub controller between the two would make sense if there is something the rpi is doing that is breaking it. I may try and use an old version of klipper and see if there is a bug introduced in a recent version.

—Reply to this email directly, view it on GitHub, or unsubscribe.You are receiving this because you commented.Message ID: ***@***.***>

Bersaker, 2025-05-13:
I have exactly the same problem with the skrmini e3v3 and the ebb42. If I connect both usb connections with the rpi4b he does not boot. If I pull a plug, it starts to boot. Does anyone know why the pi4b does this?
I tried the zero w2, rpi3b, rpi3b+ and rpi5. Everything works without any problems.
There must be a solution for the pi4b...

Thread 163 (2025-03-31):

Sb2209 USB - USB camera does not connect

volt64bolt, 2025-03-31:
Hi,
Using sb2209 USB ver. With klipper connected to an rpi 3b+

When connecting a USB camera it does not connect and the rpi throws the following errors in dmesg

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

The same camera works on a Windows computer or directly on the pi.
I have also tried 3 other cameras with the same error.

bigtreetech, 2025-03-31:
You must ensure that the cable from the USB port to the camera is shielded otherwise you may get communication errors. You will need to manually crimp the shield into the GND terminal of the JST connector and ensure that the shield travels the length of the cable until the camera.

volt64bolt, 2025-03-31:
Thank you, it is a shielded cable however I did forget to ground it. I will try this and get back to you

volt64bolt, 2025-03-31:
I managed to resolve it, turns out both the front facing usb headers have dodgy earths, moved it to the one next to the main connector and it worked straight away.

Closed 2025-03-31.

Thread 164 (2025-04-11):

Lost communication with MCU 'EBBCan' after 1-3 minuts of printing

ZlobniyDaemon, 2025-04-11:
Recently encountered the following problem:
After 1–3 minutes of printing, the connection with the EBB SB2209 RP2040 is lost and the printer shuts down.
This issue only occurs during printing. In all other situations (toolhead movements, hotend or heat bed heating, filament extrusion), no errors occur.

SB2209 is connected to Octopus Pro V1.1 via CAN. I also tried connecting through BTT U2C, changing the CAN cable, flashing the controller, but the error persists and only occurs during printing.

[klippy (1).log](https://github.com/user-attachments/files/19706790/klippy.1.log)

bigtreetech, 2025-04-11:
It seems like you may have one of two issues:

1. Poor strain relief on the connector leading to comms failures while moving - Using a cable tie around the connector and the socket to lock it in place can help with this.
2. ESD discharge into the EBB resulting in an MCU reset and a disconnect event. To solve this you can have a look at the EBB SB2209 USB manual where there is a section on grounding.

ZlobniyDaemon, 2025-04-11:
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

bigtreetech, 2025-04-11:
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

ESD can affect both USB and CAN.

Also, even a printed strain relief can result in poor connection. Cable ties are the sure way of removing this variable.

ZlobniyDaemon, 2025-04-11:
> ESD can affect both USB and CAN.

Looking [this manual ](https://github.com/bigtreetech/EBB/blob/master/EBB_SB2209_USB/Manual/BIGTREETECH%20EBB%20SB2209%20USB%20V1.0%20User%20Manual.pdf) for grounding information and can't find it. What page i need?

> Also, even a printed strain relief can result in poor connection. Cable ties are the sure way of removing this variable.
In that case, the loss of communication would occur during other movements, such ashoming, input shamer calibration, testing max speed and acceleralions.

ZlobniyDaemon, 2025-04-11:
> https://github.com/bigtreetech/EBB/blob/master/EBB_SB2209_USB/Manual/BIGTREETECH%20EBB%20SB2209%20USB%20V1.2%20User%20Manual.pdf

I followed the grounding instructions, and the connection losses have stopped. I'm still monitoring, but the printing has been running for an hour without any issues.
Perhaps a similar section on grounding should be added to the SB2206 CAN manual?

oleksii-suprun, 2025-08-11:
I have the same issue and am looking for help with fixing it. I have BTT Manta M8P 2.0 connected to EBB SB2209 CAN V1.0 (RP2040) with CAN. Randomly, I'm getting an error "Lost communication with MCU 'EBBCan' Once the underlying issue is corrected, use the "FIRMWARE_ RESTART" command to reset the firmware, reload the config, and restart the host software. Printer is shutdown". This could happen after 3 minutes of printing or after 30-40 minutes.

What I've tried/did so far:
1. Upgraded Klipper to the latest version, flashed the latest version of firmware.
2. As was talked about above, I added grounding for the extruder motor.
3. Unfolded the CAN cable and removed it from the case.
4. Tried checked connections, detached/reattached cables.
5. Disassembled and assembled the toolhead to make sure the extrusion is smooth.
6. Verified voltage on the PCU during the print - stable 24.2V, no drops.
8. Bought another EBB SB2209 CAN V1.0 (RP2040) + cable and replaced everything (board and cable one by one).

But nothing from above helped. Random disconnects continue. Another thing I noticed is that it looks like the toolhead continues moving even after the filament has already stopped extruding. The following picture demonstrates this.

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

I also noticed that all stops occur during the solid infill printing.

I'm attaching logs and my assembly photo (I use a cable fastening clip "EBB SB2240_2209 CAN/CAD/Printed_Part_for_CAN_Cable_V1.2.STEP" to immobilize the connection, but it is detached in this photo).

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

Log files:

- [klippy.log](https://github.com/user-attachments/files/21709366/klippy.log)
- [moonraker.log](https://github.com/user-attachments/files/21709373/moonraker.log)

Closed 2025-04-11.

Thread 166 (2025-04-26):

SB2209 RP2204 gpio21 and gpio22 always triggered

ZlobniyDaemon, 2025-04-26:
I am trying to connect filament sensors to GPIO21 and GPIO22, but the sensor signal does not change when they are triggered.

`[filament_switch_sensor Aft_Extruder]
pause_on_runout: false
#   When set to True, a PAUSE will execute immediately after a runout
#   is detected. Note that if pause_on_runout is False and the
#   runout_gcode is omitted then runout detection is disabled. Default
#   is True.
runout_gcode:
    PAUSE
    RESPOND TYPE=error MSG="Обнаружено отсутствие прутка после экструдера"
#   A list of G-Code commands to execute after a filament runout is
#   detected. See docs/Command_Templates.md for G-Code format. If
#   pause_on_runout is set to True this G-Code will run after the
#   PAUSE is complete. The default is not to run any G-Code commands.
insert_gcode:
    RESPOND TYPE=error MSG="Обнаружена подача прутка"
#   A list of G-Code commands to execute after a filament insert is
#   detected. See docs/Command_Templates.md for G-Code format. The
#   default is not to run any G-Code commands, which disables insert
#   detection.
event_delay: 3
#   The minimum amount of time in seconds to delay between events.
#   Events triggered during this time period will be silently
#   ignored. The default is 3 seconds.
#pause_delay: 0.5
#   The amount of time to delay, in seconds, between the pause command
#   dispatch and execution of the runout_gcode. It may be useful to
#   increase this delay if OctoPrint exhibits strange pause behavior.
#   Default is 0.5 seconds.
switch_pin: EBBCan:gpio21
#   The pin on which the switch is connected. This parameter must be
#   provided.`

I have several SB2209 RP2204 boards, and I am experiencing the same issue with all of them.

cruzer619, 2025-05-19:
please reference #88 for solution.

ZlobniyDaemon, 2025-05-20:
> please reference [#88](https://github.com/bigtreetech/EBB/issues/88) for solution.

Okay, let's say adding a resistor to GPIO21 works (though it's unclear why the pin doesn't work out of the box on the RP2040 but works on STM). What about GPIO22? It also doesn't work—should I solder a second resistor to it as well?

ZlobniyDaemon, 2025-05-20:
> "^EBBCan:gpio22" so like that

Didn't work foк me

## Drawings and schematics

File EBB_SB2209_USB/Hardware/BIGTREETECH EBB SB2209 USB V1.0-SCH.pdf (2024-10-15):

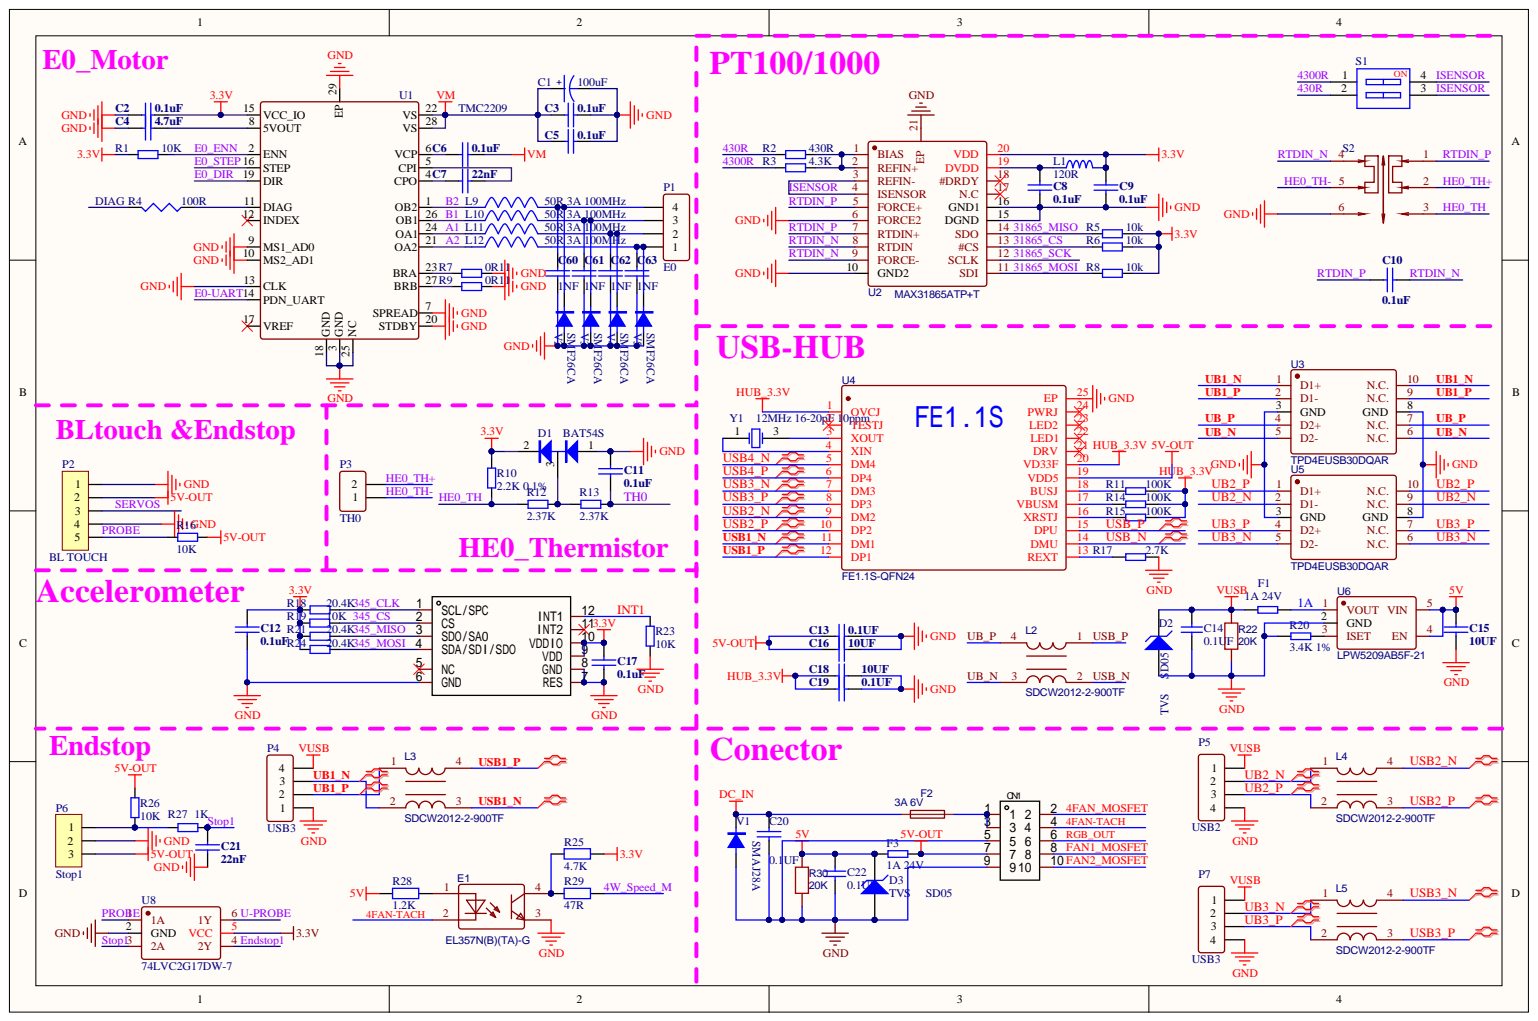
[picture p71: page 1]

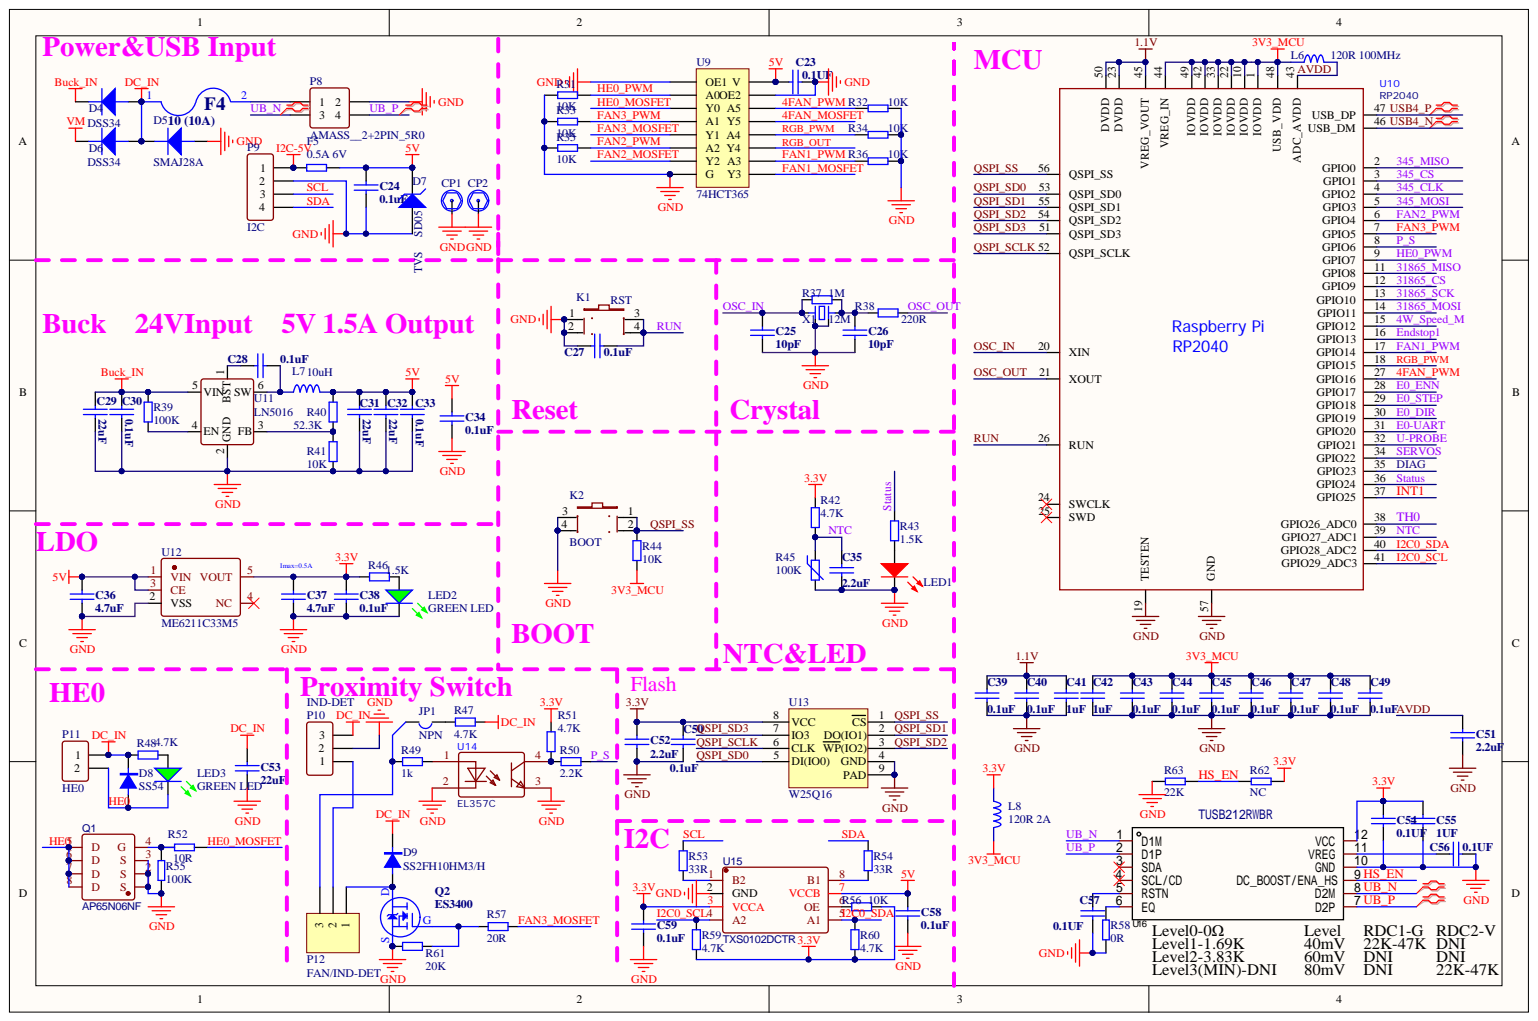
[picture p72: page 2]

Proximity Switch R47 IND-DET GND 3.3V | Flash 3.3V U13

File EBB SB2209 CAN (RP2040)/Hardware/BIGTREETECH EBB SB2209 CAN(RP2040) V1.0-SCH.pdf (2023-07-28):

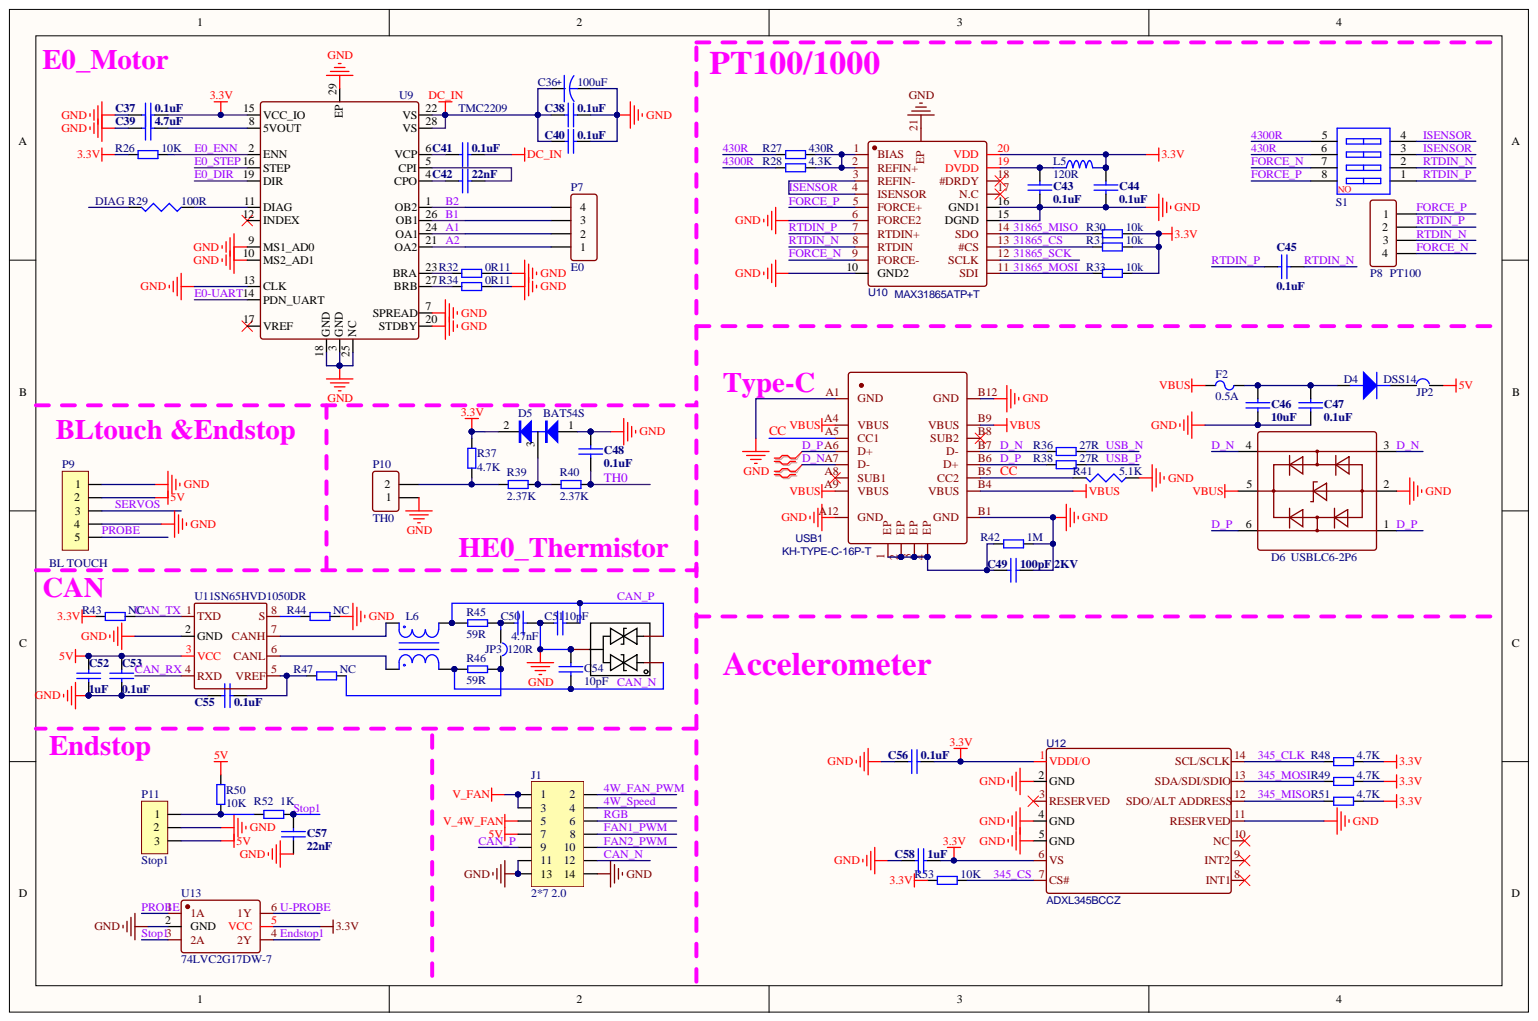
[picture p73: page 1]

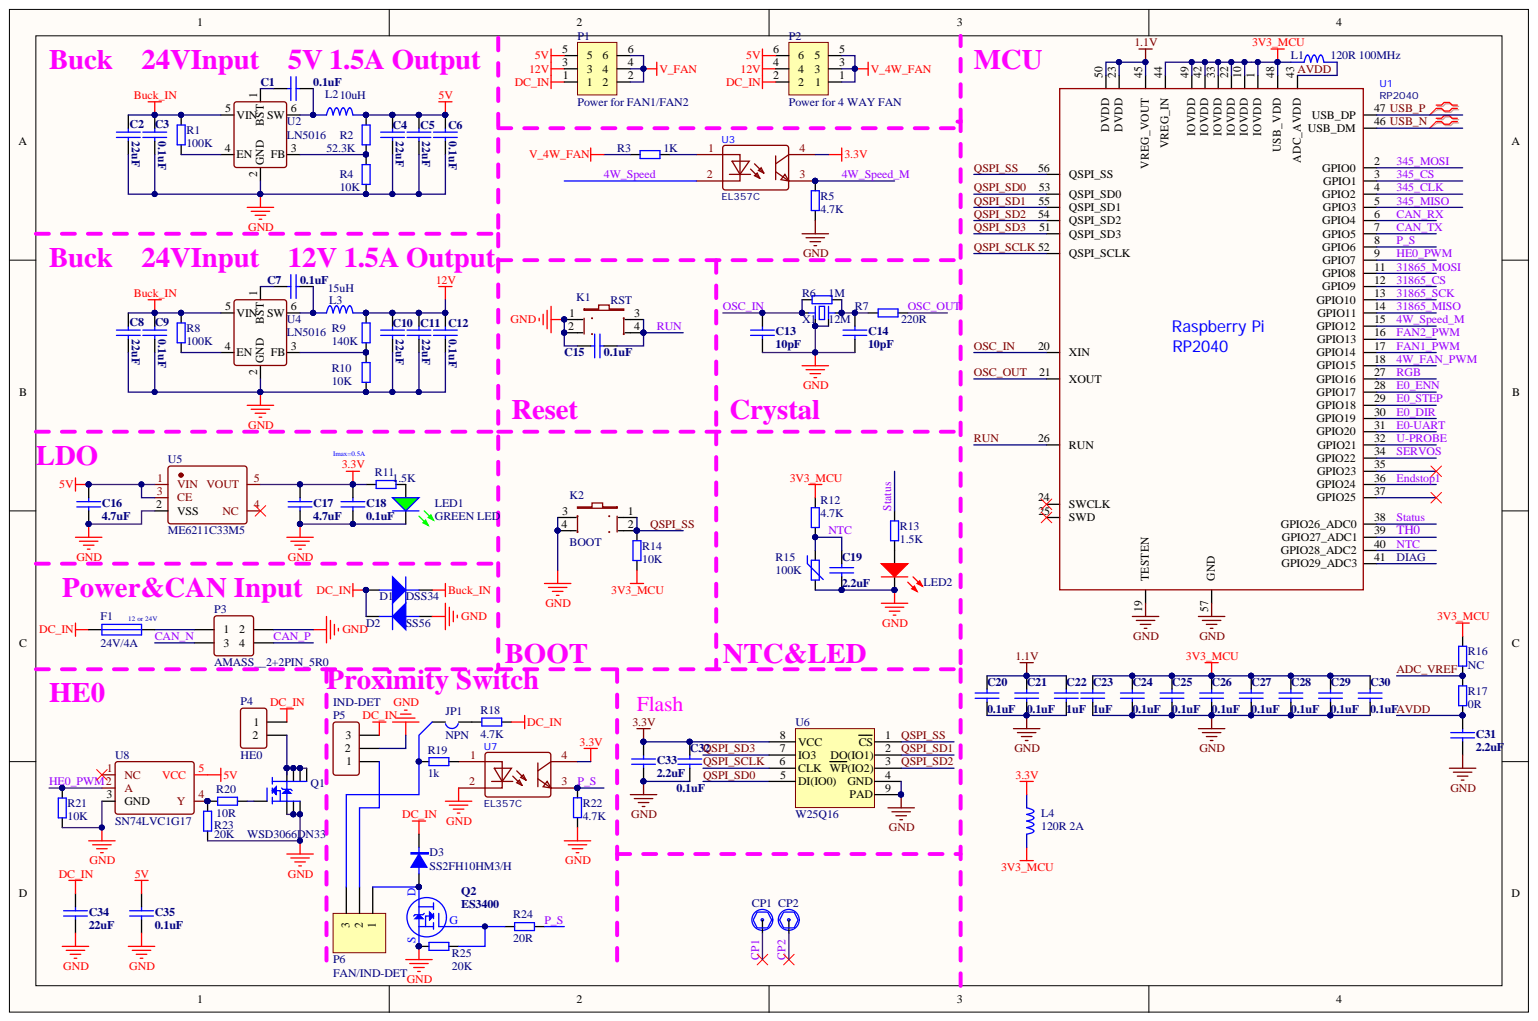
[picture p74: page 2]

Power for 4 WAY FAN

Proximity Switch R18 IND-DET GND JP1 | Flash 3.3V U6

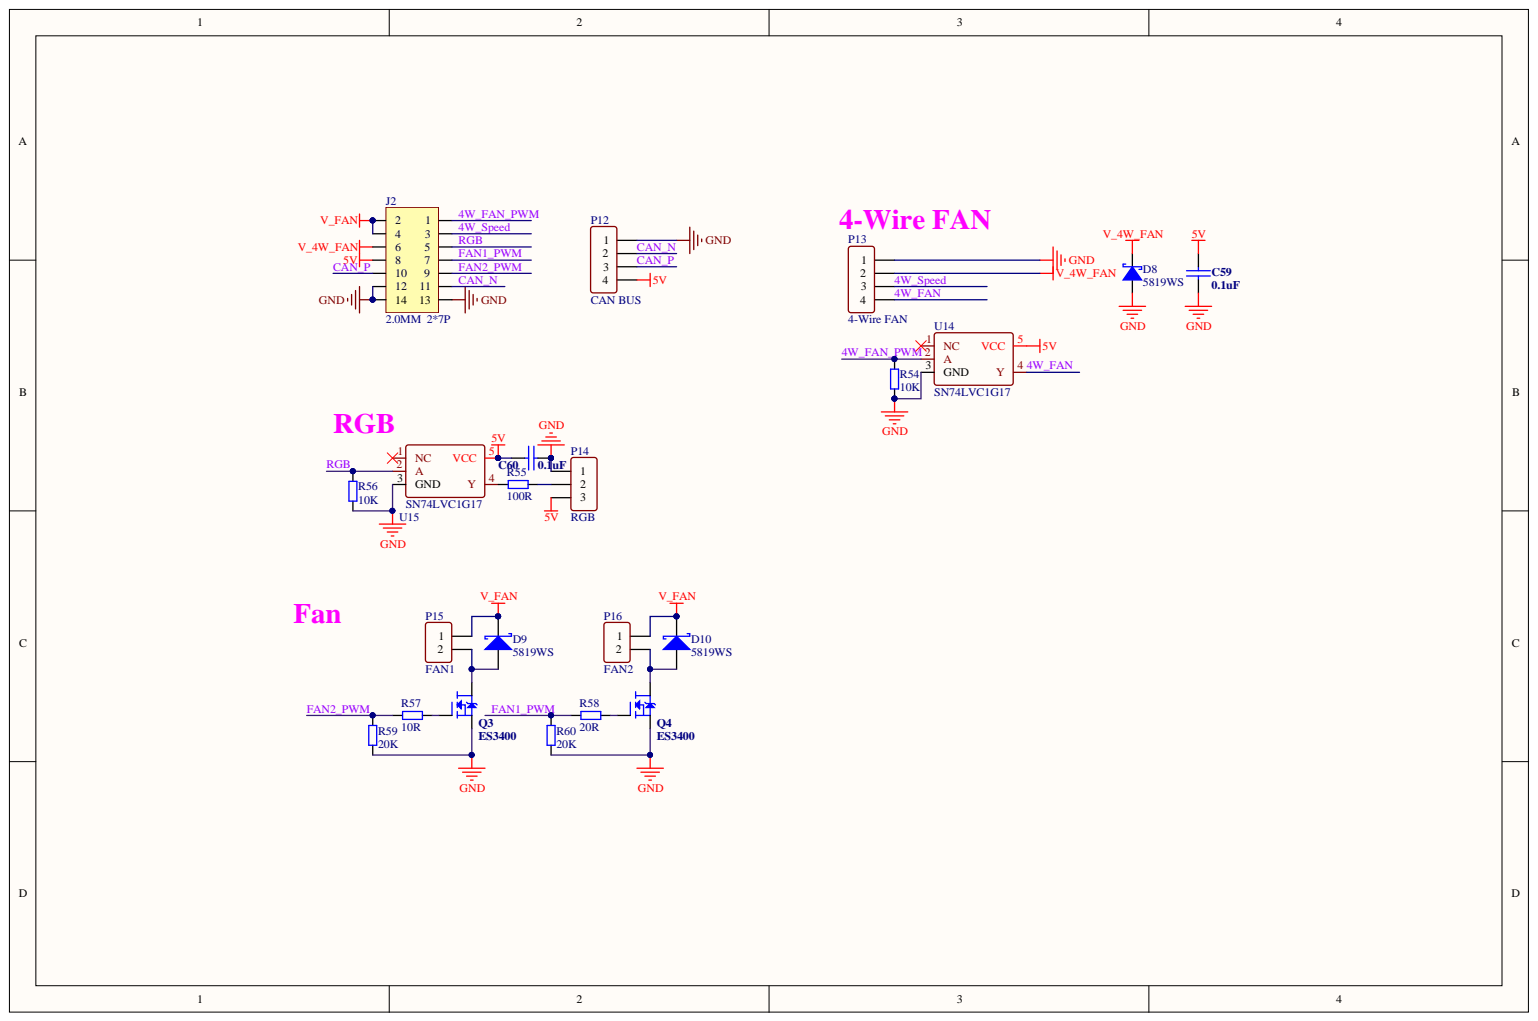
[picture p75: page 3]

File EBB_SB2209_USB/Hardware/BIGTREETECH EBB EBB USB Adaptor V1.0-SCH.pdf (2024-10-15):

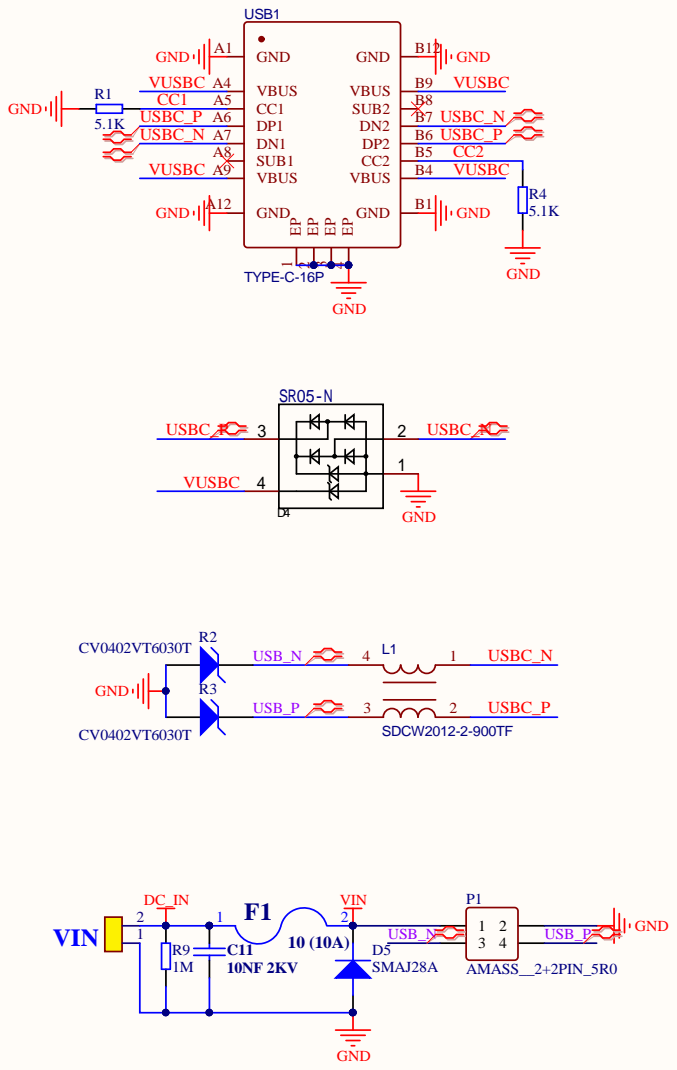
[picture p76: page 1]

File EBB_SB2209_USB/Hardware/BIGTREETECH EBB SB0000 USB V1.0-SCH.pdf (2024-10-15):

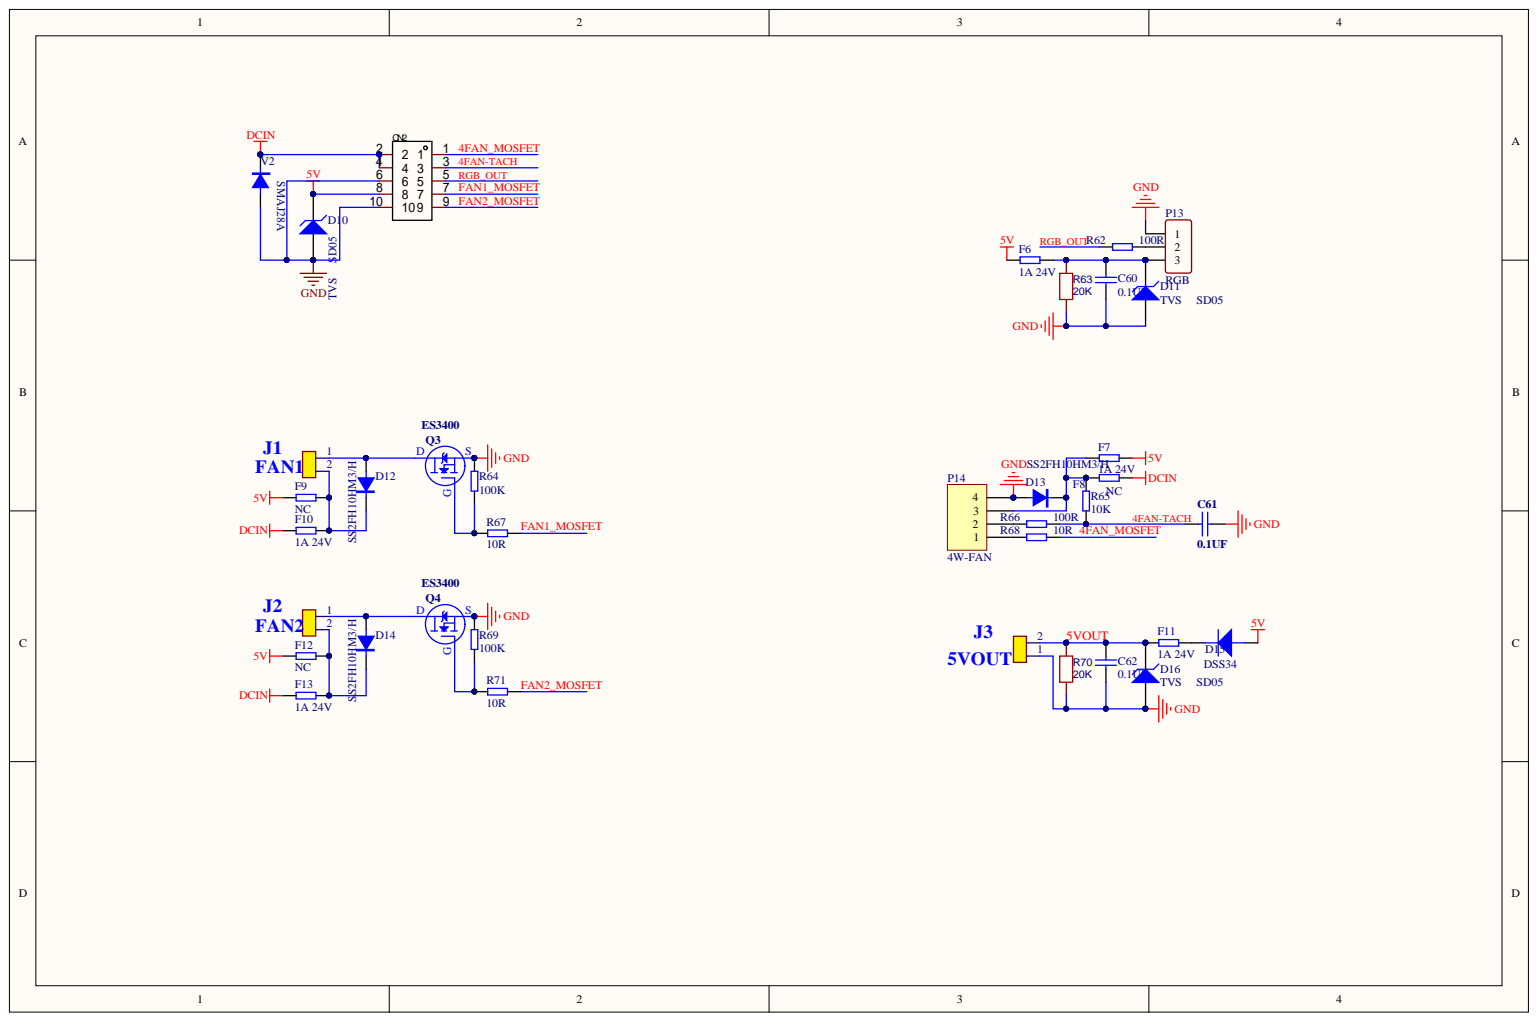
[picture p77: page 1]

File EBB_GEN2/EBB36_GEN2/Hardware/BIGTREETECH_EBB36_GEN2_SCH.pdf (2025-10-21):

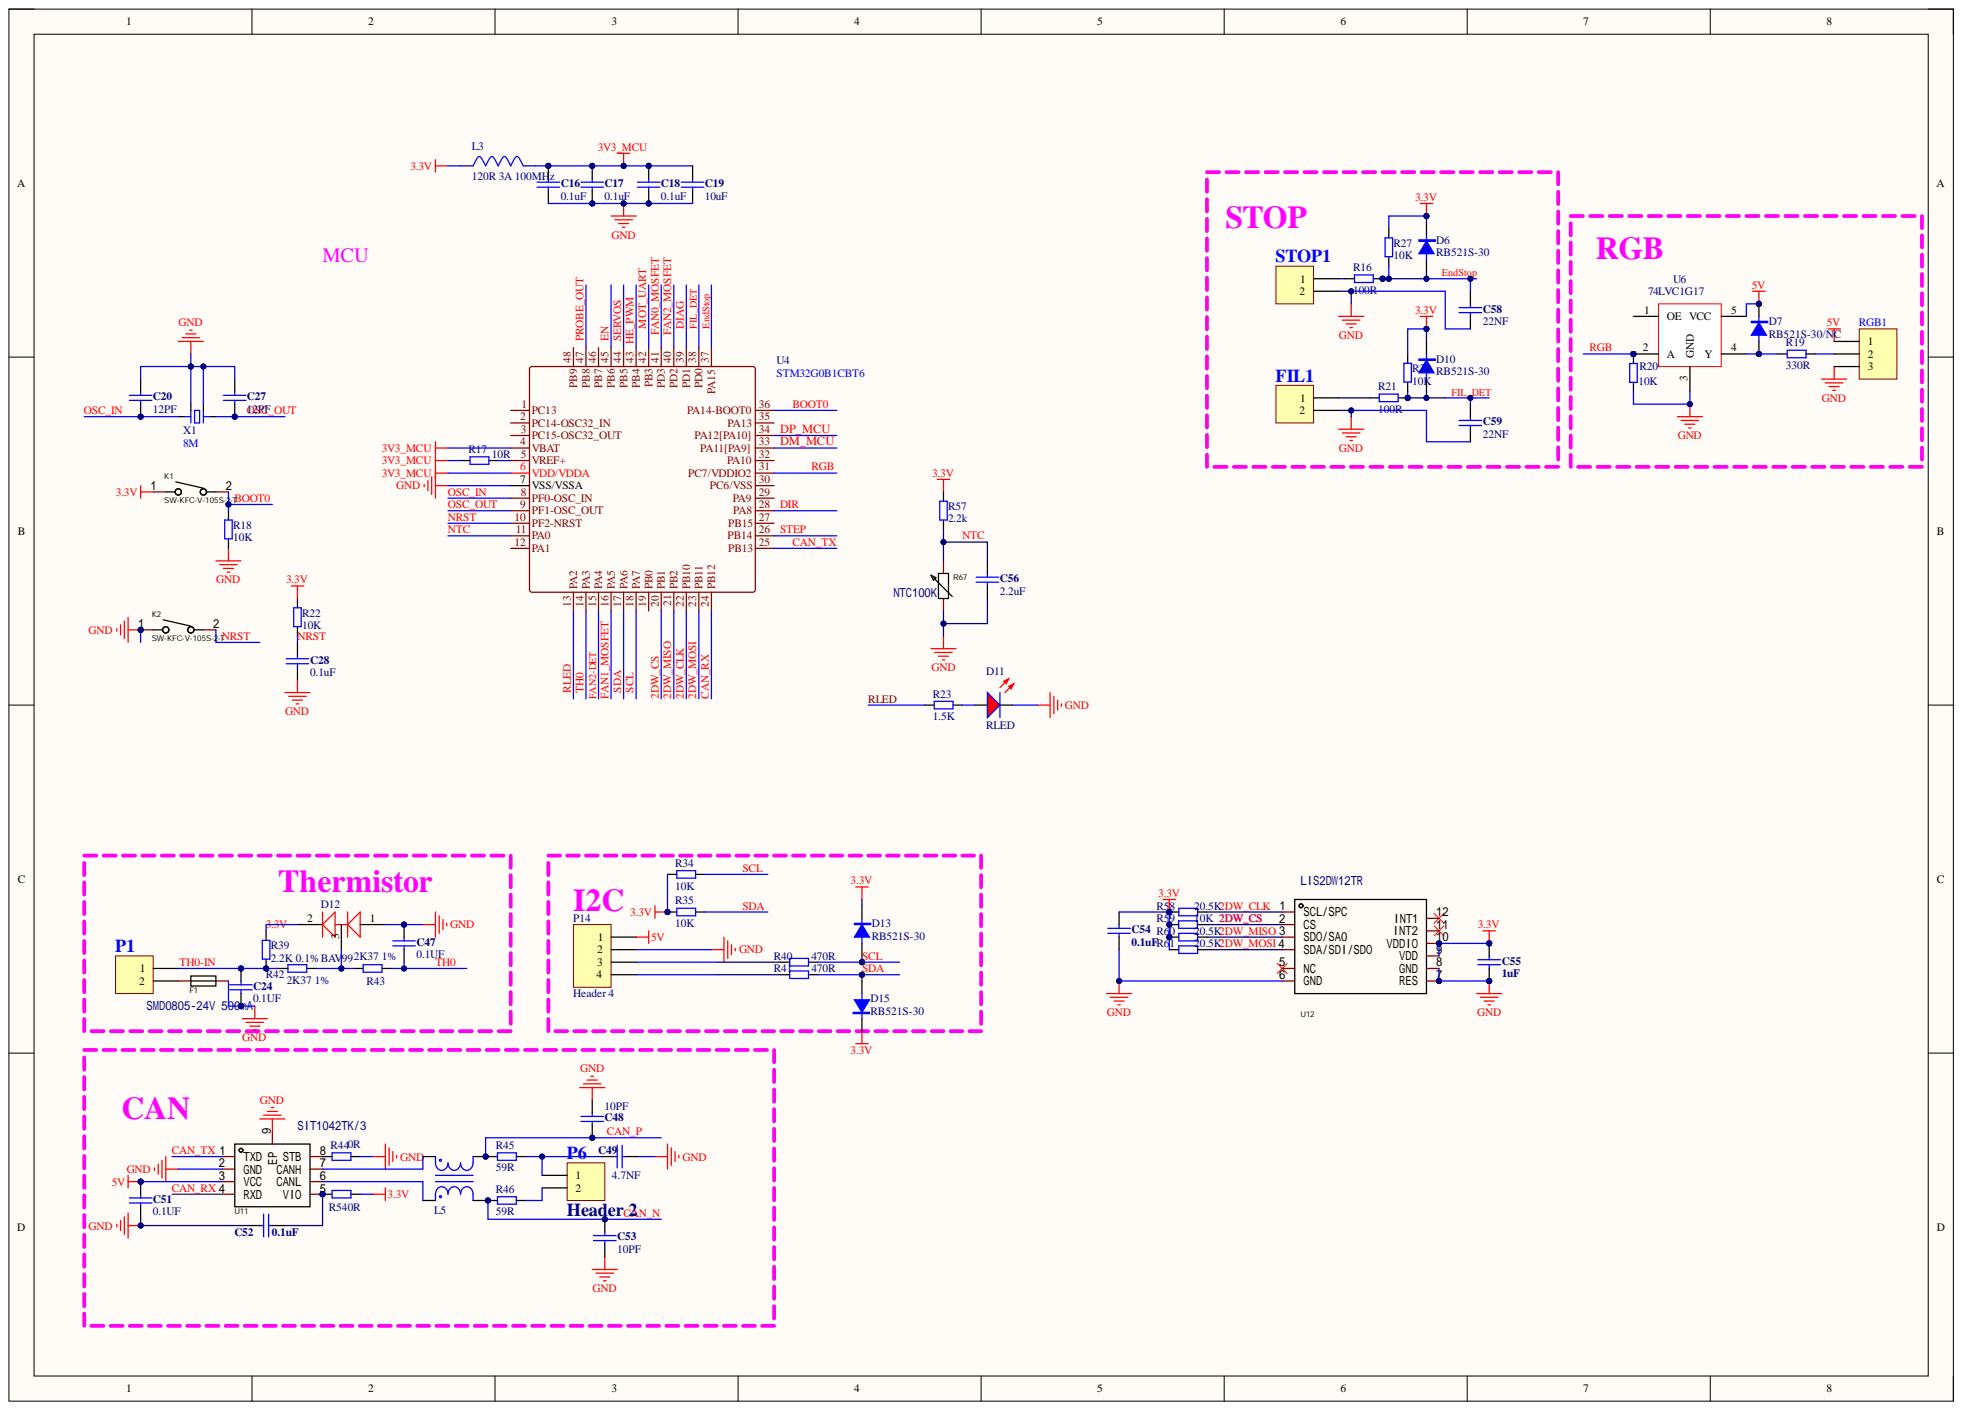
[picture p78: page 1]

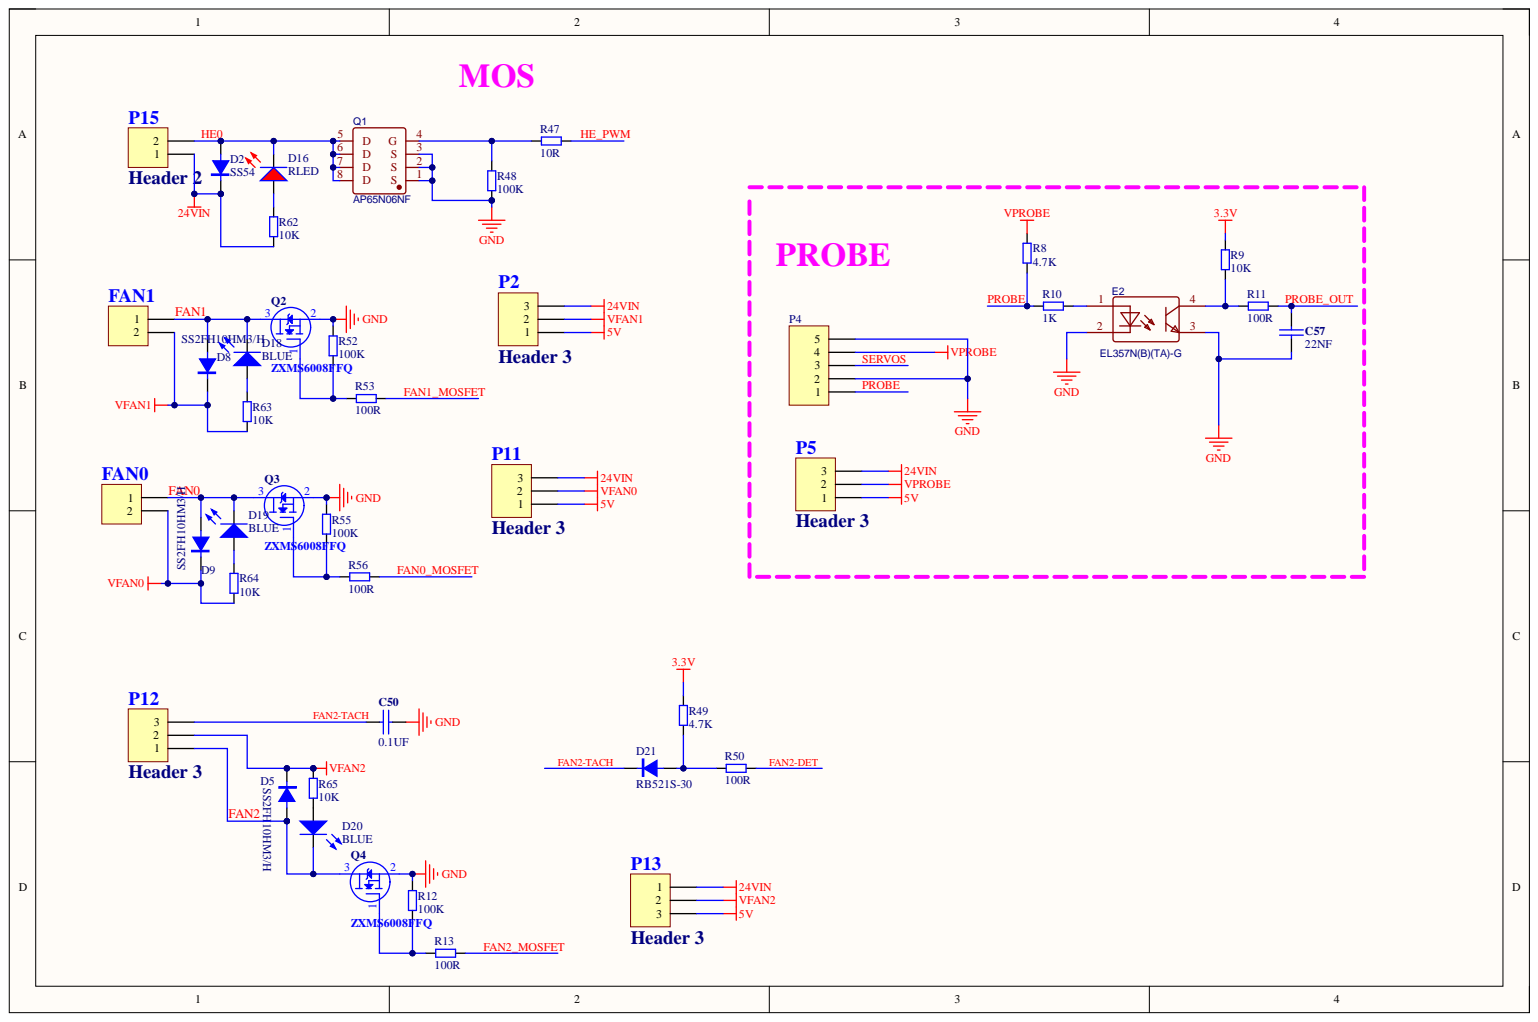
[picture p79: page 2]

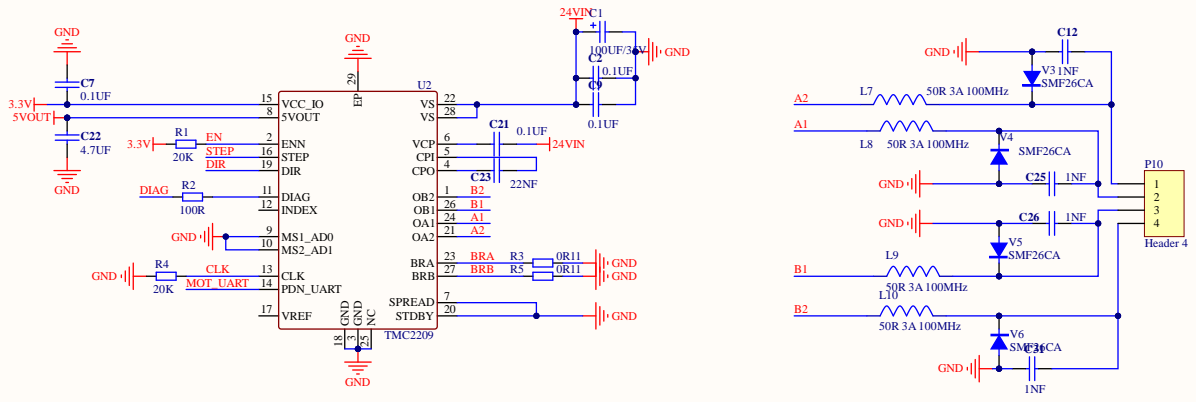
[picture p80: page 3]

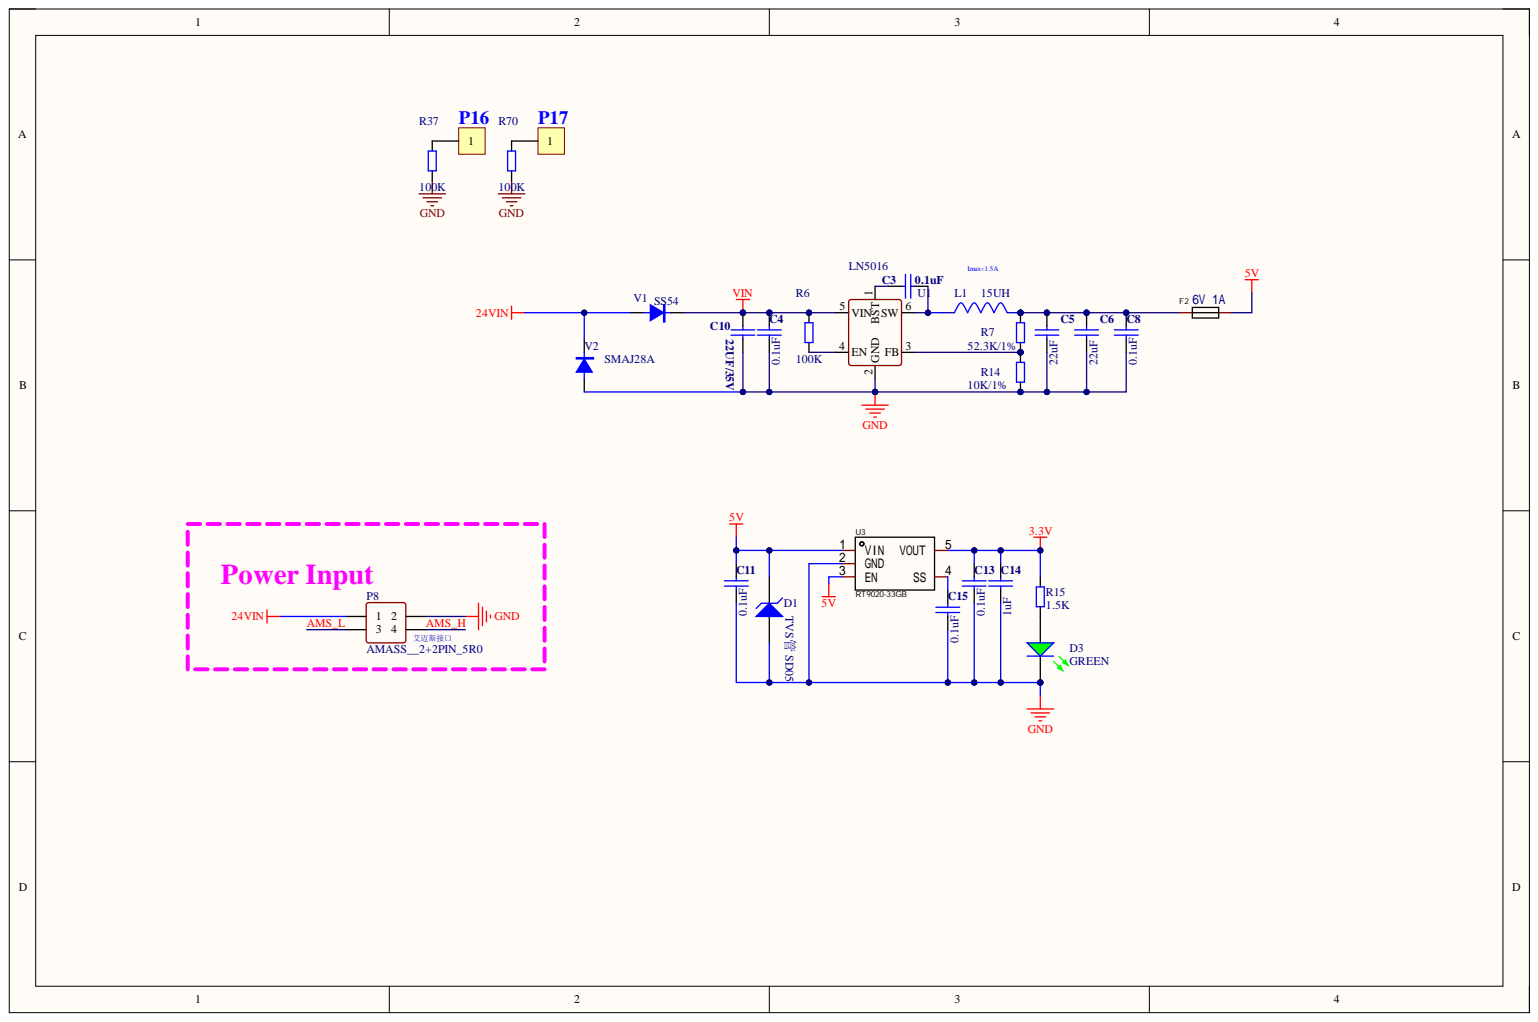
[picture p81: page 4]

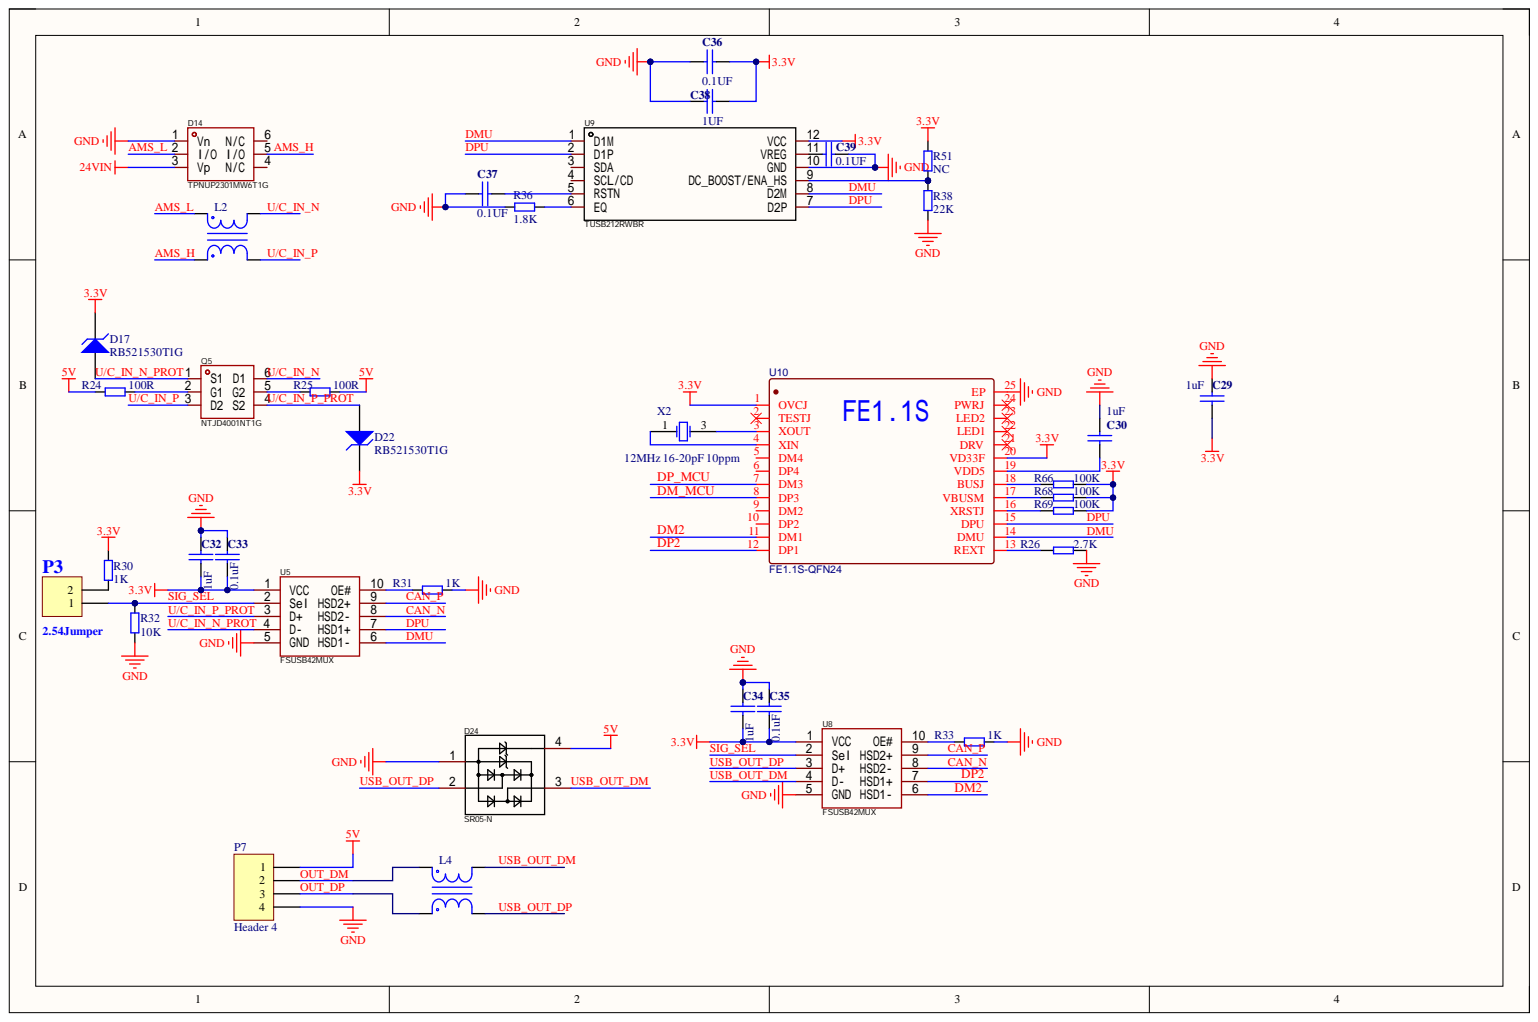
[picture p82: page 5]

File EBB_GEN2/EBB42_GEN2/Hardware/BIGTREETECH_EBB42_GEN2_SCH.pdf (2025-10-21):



FAN2




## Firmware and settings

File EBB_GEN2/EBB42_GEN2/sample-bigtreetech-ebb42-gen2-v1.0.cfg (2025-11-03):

# This file contains common pin mappings for the BIGTREETECH EBB42
# GEN2 board. To use this config, the firmware should be compiled for the
# STM32G0B1 with "8 MHz crystal" and "USB (on PA11/PA12)" or "CAN bus (on PB12/PB13)" .
# The "EBB42 GEN2" micro-controller will be used to control the components on the nozzle.

# See docs/Config_Reference.md for a description of parameters.

[mcu EBB]
serial: /dev/serial/by-id/usb-Klipper_Klipper_firmware_12345-if00
#canbus_uuid=a62a88bb28e3

[temperature_sensor EBB42]
sensor_type: Generic 3950
sensor_pin: EBB:PA0
pullup_resistor: 2200

[lis2dw]
cs_pin: EBB:PB1
spi_bus:spi2_PB2_PB11_PB10
axes_map: x,y,z

[extruder]
step_pin: EBB:PD3
dir_pin: EBB:PD2
enable_pin: !EBB:PB6
microsteps: 16
rotation_distance: 33.500
nozzle_diameter: 0.400
filament_diameter: 1.750
heater_pin: EBB:PB0
sensor_type: EPCOS 100K B57560G104F
pullup_resistor: 2200
sensor_pin: EBB:PA1
control: pid
pid_Kp: 21.527
pid_Ki: 1.063
pid_Kd: 108.982
min_temp: 0
max_temp: 250

[tmc2209 extruder]
uart_pin: EBB:PB3
run_current: 0.650
stealthchop_threshold: 999999

#[filament_switch_sensor fil_det]
#switch_pin: EBB:PA3

[fan]
pin: EBB:PB8

[heater_fan hotend_fan]
pin: EBB:PB15
heater: extruder
heater_temp: 50.0

#[heater_fan 3w_fan2]
#pin: EBB:PB4
#tachometer_pin: EBB:PB9

#[neopixel hotend_rgb]
#pin: EBB:PB14

#[bltouch]
#sensor_pin: ^!EBB:PA5
#control_pin: EBB:PA4

#[output_pin rled]
#pin:EBB:PA8

#[temperature_sensor BME280]
#sensor_type: BME280
#i2c_mcu: EBB
##i2c_bus: i2c1_PA9_PA10
#i2c_software_scl_pin: EBB:PA9
#i2c_software_sda_pin: EBB:PA10

#endstop_pin: EBB:PA2
#diag_pin: ^EBB:PD1

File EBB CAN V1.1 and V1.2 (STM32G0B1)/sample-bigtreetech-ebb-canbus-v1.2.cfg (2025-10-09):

# This file contains common pin mappings for the BIGTREETECH EBBCan
# Canbus board. To use this config, the firmware should be compiled for the
# STM32G0B1 with "8 MHz crystal" and "USB (on PA11/PA12)" or "CAN bus (on PB0/PB1)".
# The "EBB Can" micro-controller will be used to control the components on the nozzle.

# See docs/Config_Reference.md for a description of parameters.

[mcu EBBCan]
serial: /dev/serial/by-id/usb-Klipper_Klipper_firmware_12345-if00
#canbus_uuid: 0e0d81e4210c

[adxl345]
cs_pin: EBBCan: PB12
spi_bus: spi2_PB2_PB11_PB10
axes_map: x,y,z

[extruder]
step_pin: EBBCan: PD0
dir_pin: !EBBCan: PD1
enable_pin: !EBBCan: PD2
microsteps: 16
rotation_distance: 33.500
nozzle_diameter: 0.400
filament_diameter: 1.750
heater_pin: EBBCan: PB13
sensor_type: EPCOS 100K B57560G104F
sensor_pin: EBBCan: PA3
control: pid
pid_Kp: 21.527
pid_Ki: 1.063
pid_Kd: 108.982
min_temp: 0
max_temp: 250

# sensor_type:MAX31865
# sensor_pin: EBBCan: PA4
# spi_bus: spi1
# rtd_nominal_r: 100
# rtd_reference_r: 430
# rtd_num_of_wires: 2

[tmc2209 extruder]
uart_pin: EBBCan: PA15
run_current: 0.650
stealthchop_threshold: 999999

[fan]
pin: EBBCan: PA0

[heater_fan hotend_fan]
pin: EBBCan: PA1
heater: extruder
heater_temp: 50.0

#[neopixel hotend_rgb]
#pin: EBBCan:PD3

#[bltouch]
#sensor_pin: ^EBBCan:PB8
#control_pin: EBBCan:PB9

#[filament_switch_sensor switch_sensor]
#switch_pin: EBBCan:PB4

#[filament_motion_sensor motion_sensor]
#switch_pin: ^EBBCan:PB3

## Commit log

2022-05-04 add EBB CAN V1.0 (stm32f072)
    [sample-bigtreetech-ebb-canbus-v1.0.cfg]
2022-05-19 add EBB CAN V1.1 (stm32g0b1)
    [sample-bigtreetech-ebb-canbus-v1.1.cfg]
2022-05-21 fix wrong pin info
2022-06-16 more detail pinout
    [sample-bigtreetech-ebb-canbus-v1.2.cfg]
2023-01-10 add EBB Voron-Stealthburner version stl
    [CW2 Cable Bridge.STEP, CW2 Cable Bridge.STL, Printed Part for CAN Cable.STEP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]
2023-01-12 update EBB SB2240/2209 info
    [sample-bigtreetech-ebb-sb-canbus-v1.0.cfg]
2023-01-12 update stl
    [Cable Clip Printed Part.STEP, Cable Clip Printed Part.STL, Printed Part for CAN Cable.STEP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]
2023-02-02 update step
    [CW2 Cable Bridge.STL, Cable Clip Printed Part.STEP, Cable Clip Printed Part.STL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]
2023-02-23 update tmc2240 cfg
    [sample-bigtreetech-ebb-sb-canbus-v1.0.cfg]
2023-03-07 fix axes_map for voron
    [sample-bigtreetech-ebb-sb-canbus-v1.0.cfg]
2023-03-08 match the port on manual, FAN1 for hotend fan, FAN2 for part cooling fan
    [sample-bigtreetech-ebb-sb-canbus-v1.0.cfg]
2023-04-19 Added custom SB parts for better thermistor wire access (#40)
    [cable_door_EBB_SB.stl, main_body_EBB_SB.stl]
2023-05-11 update manual cable picture
2023-06-06 add EBB SB RP2040 version
    [sample-bigtreetech-ebb-sb-rp2040-canbus-v1.0.cfg]
2023-06-26 upload EBB SB stls
    [Cable_Cover_for_Pcb_v1.1.STEP, Cable_Cover_for_Pcb_v1.1.STL, Printed_Part_for_CAN_Cable_v1.1.STEP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]
2023-08-25 Added custom SB parts STEP files (#63)
    [cable_door_EBB_SB.step, cable_door_EBB_SB.stl, cable_door_PCB_EBB_SB.step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]
2023-11-21 update klipper.bin firmware to the last version and all canbus speed set to 1M
2024-02-19 Rename Main_Body_V1.2.STEP to Main_Body_EBB.STEP (#102)
    [Main_Body_EBB.STEP]
2024-02-19 Rename Cable_Cover_For_PCB_V1.2.STEP to Cable_Cover_EBB.STEP (#101)
    [Cable_Cover_EBB.STEP]
2024-02-19 Rename Main_Body_V1.2.stl to Main_Body_EBB.stl (#100)
    [Main_Body_EBB.stl, Main_Body_V1.2.stl]
2024-02-19 Rename Cable_Cover_For_PCB_V1.2.stl to Cable_Cover_EBB.stl (#99)
    [Cable_Cover_EBB.stl]
2024-03-18 Update Main_Body_EBB STL (#111)
    [Main_Body_EBB.stl]
2024-06-20 Fixed main body of SB to reflect the lastest version.
    [Main_Body_EBB.stl]
2024-07-02 updated dir naming to make V1.2 more clear
    [sample-bigtreetech-ebb-canbus-v1.1.cfg, sample-bigtreetech-ebb-canbus-v1.2.cfg]
2024-07-03 CAN bus recommendation speed increased from 250K to 1M
2024-07-25 add EBB SB2209 USB
    [Cable_Anchor_EBB-SB-USB.step, Cable_Anchor_EBB-SB-USB.stl, Cable_Cover_EBB-SB-USB.STEP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]
2024-07-30 add ebb sb usb manual and config
    [sample-bigtreetech-ebb-sb-usb-v1.0.cfg]
2024-07-30 fix .cfg
    [sample-bigtreetech-ebb-sb-usb-v1.0.cfg]
2024-09-03 Added mount for adapter PCB
    [EBB_SB2209_ADAPTER_BASE.stl, EBB_SB2209_ADAPTER_TOP.stl]
2024-09-10 Arranging files in prep for upload of new printable models for additional extruder support
    [Cable_Anchor_EBB-SB-USB.step, Cable_Anchor_EBB-SB-USB.stl, Cable_Cover_EBB-SB-USB.STEP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]
2024-09-10 Add readme to explain current Galileo2 extruder support
2024-10-09 Added beta galileo 2 mount
    [Galileo 2 Extruder BODY -EBB USB.STEP, Galileo 2 Extruder Cable_Cover-EBB USB.STEP, Galileo 2 Extruder Chain_Anchor -EBB USB.STEP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]
2025-02-10 add ebb sb2209 usb stls
    [Cable_Cover_For_EBBSB1.STEP, Cable_Cover_For_EBBSB1.STL]
2025-02-13 Changed location of airflow covers
    [Cable_Cover_For_EBBSB1.STEP, Cable_Cover_For_EBBSB1.STL]
2025-03-04 Added enhanced airflow cover for EBB USB Galileo 2 version
    [Galileo 2-EBB USB.3mf, galileo 2 extruder cable_cover-ebb usb1_enhanced_airflow.STEP]
2025-10-09 Modify software SPI to hardware SPI
    [sample-bigtreetech-ebb-canbus-v1.1.cfg, sample-bigtreetech-ebb-canbus-v1.2.cfg, sample-bigtreetech-ebb-sb-canbus-v1.0.cfg]
2025-10-18 add EBB GEN2
    [sample-bigtreetech-ebb36-gen2-v1.0.cfg, sample-bigtreetech-ebb42-gen2-v1.0.cfg]
2025-11-03 Fix wrong heater fan pin configuration in EBB42 GEN2 config file
    [sample-bigtreetech-ebb42-gen2-v1.0.cfg]
2025-11-03 Fix wrong FIL_DET pin in EBB36 GEN2 pinout picture
2025-11-21 fix description in pin diagram
2025-11-22 Fix header formatting in readme.md
    Added a space between '#' and 'CAD' for formatting.
